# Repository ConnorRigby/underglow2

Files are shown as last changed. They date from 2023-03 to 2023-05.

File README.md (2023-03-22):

# Underglow 2

Automotive PMU designed for controlling external lighting.

## Specs

|high side output|low side output|12v digital input|BLE|Radio|
|-|-|-|-|-|
|2|6|4|1|1|

## Repository Structure

|folder|description|
|-|-|
|[docs](docs/README.md)|Documentation for hardware as well as 3d models and interactive bill of materials|
|[hardware](hardware/README.md)|Source material for the hardware PCB design|

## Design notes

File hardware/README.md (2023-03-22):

# coneRGB Underglow Controller Hardware Design

Source material for the PCB design. Designed using KiCAD intended to
be produced at PCBWay using parts from LCSC.

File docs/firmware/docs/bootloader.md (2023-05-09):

# coneRGB STM32 Bootloader

To facilitate over the air updates, coneRGB implements a custom bootloader.

```puml
@startuml
(*) --> "Power On Reset"

if "Update Status" then
  -left-> [started]"Enter Bootloader"
  --> copy update into flash
  -right->[jump to main application] (*)
else
  ->[no update] "Increment boot counter"
  -->[jump to main application] (*)
endif

@enduml
```

## Over The Air Update Procedure

* Initiate a firmware update over a supported transport (BLE, CAN)
* Write the entire update binary
* Initiate a reset
* The bootloader will now copy the update payload into flash

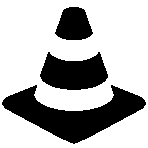
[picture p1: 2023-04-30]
assets/traffic-cone.bmp

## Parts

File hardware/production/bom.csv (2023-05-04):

Designator | Footprint | Quantity | Value | LCSC Part #
ANT601, ANT801 | IPEX-SMD_BWIPX-1-001E | 2 | BWIPX-1-001E | C496552
BT501 | BAT-SMD_CR1220-2 | 1 | Battery_Cell | C70381
C201, C301, C302, C303, C304, C305, C306, C307, C308, C309, C310, C605, C816 | 805 | 13 | C_0805_10u_X5R | C162422
C202, C603 | 805 | 2 | C_0805_1u_X7R | C24123
C401, C402, C502, C503, C504, C505, C506, C507, C508, C509, C511, C516, C519, C520, C521, C606, C607, C610, C611, C612, C808, C809, C810, C813 | 402 | 24 | C_0402_100nf_X7R | C110251
C501 | 805 | 1 | C_0805_4u7_X5R | C577033
C510 | 402 | 1 | C_0402_1u_X5R | C307413
C512, C513 | 402 | 2 | C_0402_2u2_X5R | C385032
C514, C515, C517, C518, C615, C616, C617, C618, C803, C811, C812 | 402 | 11 | C_0402_22p_C0G | C161315
C604, C801 | 402 | 2 | C_0402_10n_C0G | C60133
C608, C609 | 402 | 2 | C_0402_1p8_C0G | C76903
C802 | 402 | 1 | C_0402_8p2_C0G | C88898
C805 | 402 | 1 | C_0402_6p8_C0G | C354360
C807 | 402 | 1 | C_0402_3p3_C0G | C76968
C814 | 402 | 1 | C_0402_5p6_C0G | C88895
C815, L803, L804 | 402 | 3 | L_0402_5n6 | C91626
C823, C825 | 402 | 2 | C_0402_100p_C0G | C711072
C828, C829 | 402 | 2 | C_0402_1nf_X7R | C126538
D201, D504, D506 | 603 | 3 | LED_0603_RED | C389517
D202, D301, D302, D505 | D_SOD-323F | 4 | 30v 230mv@100ma 1A | C146335
D501 | SOT-23 | 1 | BAT54C | C5184395
D502 | 603 | 1 | LED_0603_GREEN | C389519
D503 | 603 | 1 | LED_0603_YELLOW | C72038
F201 | 1206 | 1 | nSMD010 | C70065
FB501 | 402 | 1 | FerriteBead_Small | C102745
L601, L802 | 402 | 2 | L_0402_22n | C86129
L602 | 402 | 1 | L_0402_3n3 | C341785
L801 | 402 | 1 | L_0402_2n7 | C98058
Q202, Q301 | SOP-8_3.76x4.96mm_P1.27mm | 2 | AO4803A | C5224315
Q302, Q303, Q304 | SOT-23-6 | 3 | 8205A | C2762931
Q801 | SOT-23 | 1 | BC817 | C39828
R201, R602 | 603 | 2 | R_0603_499 | C137714
R203, R206 | 805 | 2 | R_0805_10k | C17414
R207 | 805 | 1 | R_0805_4k7 | C17673
R301, R302, R701, R703, R705, R707 | 603 | 6 | R_0603_100k | C335088
R401 | 1206 | 1 | R_1206_120 | C294122
R402, R503, R504, R505, R608, R805 | 402 | 6 | R_0402_10k | C2902636
R501, R802, R803 | 402 | 3 | R_0402_100k | C2984406
R502, R601, R804 | 402 | 3 | R_0402_0 | C102745
R506, R507, R508, R509 | 603 | 4 | R_0603_330 | C861328
R702, R704, R706, R708 | 603 | 4 | R_0603_20k | C319766
RN501, RN502, RN503, RN504 | R_Array_Concave_4x0402 | 4 | RA_0402_04_100 | C48442
U201 | SOT-23-5 | 1 | SPX3819M5-L-3-3_TR | C9055
U202, U301, U302, U303, U304, U305, U306, U307, U308 | SOT-23-5 | 9 | MCP1416 | C83775
U401 | SOIC-8_3.9x4.9mm_P1.27mm | 1 | TLE9251VSJXUMA1 | C189937
U501 | SOIC-8_5.23x5.23mm_P1.27mm | 1 | W25Q16JVSSIQ | C82317
U503 | LQFP-100_14x14mm_P0.5mm | 1 | STM32F407VGTx | C12345
U601 | QFN50P500X500X90-33N | 1 | ESP32-C3FH4 | C2858491
U801 | QFN-28-1EP_5x5mm_P0.5mm_EP3.75x3.75mm_ThermalVias | 1 | RF69 | C77220
U802 | SOT-23-6 | 1 | AS193-73LF | C6199
Y501 | Crystal_SMD_3225-4Pin_3.2x2.5mm | 1 | 25_Mhz | C9006
Y502, Y602 | Crystal_SMD_3215-2Pin_3.2x1.5mm | 2 | Q13FC1350000400 | C32346
Y601 | Crystal_SMD_3225-4Pin_3.2x2.5mm | 1 | 40_Mhz | C2901712
Y801 | Crystal_SMD_3225-4Pin_3.2x2.5mm | 1 | 32_Mhz | C9009

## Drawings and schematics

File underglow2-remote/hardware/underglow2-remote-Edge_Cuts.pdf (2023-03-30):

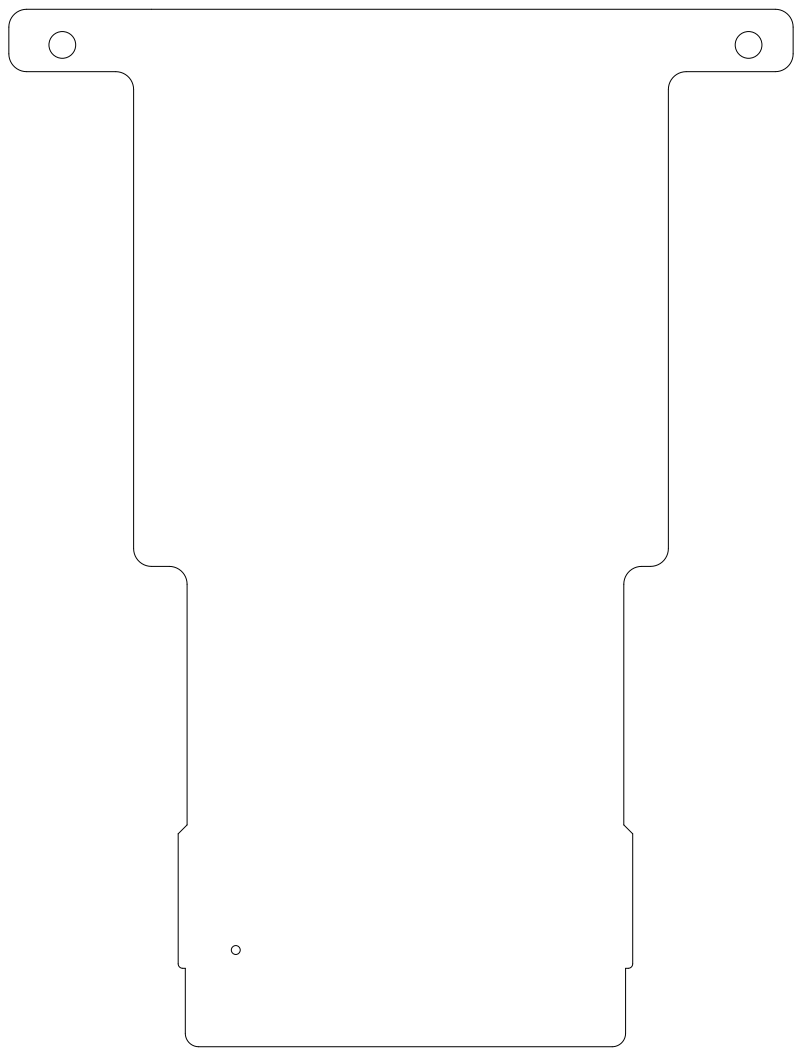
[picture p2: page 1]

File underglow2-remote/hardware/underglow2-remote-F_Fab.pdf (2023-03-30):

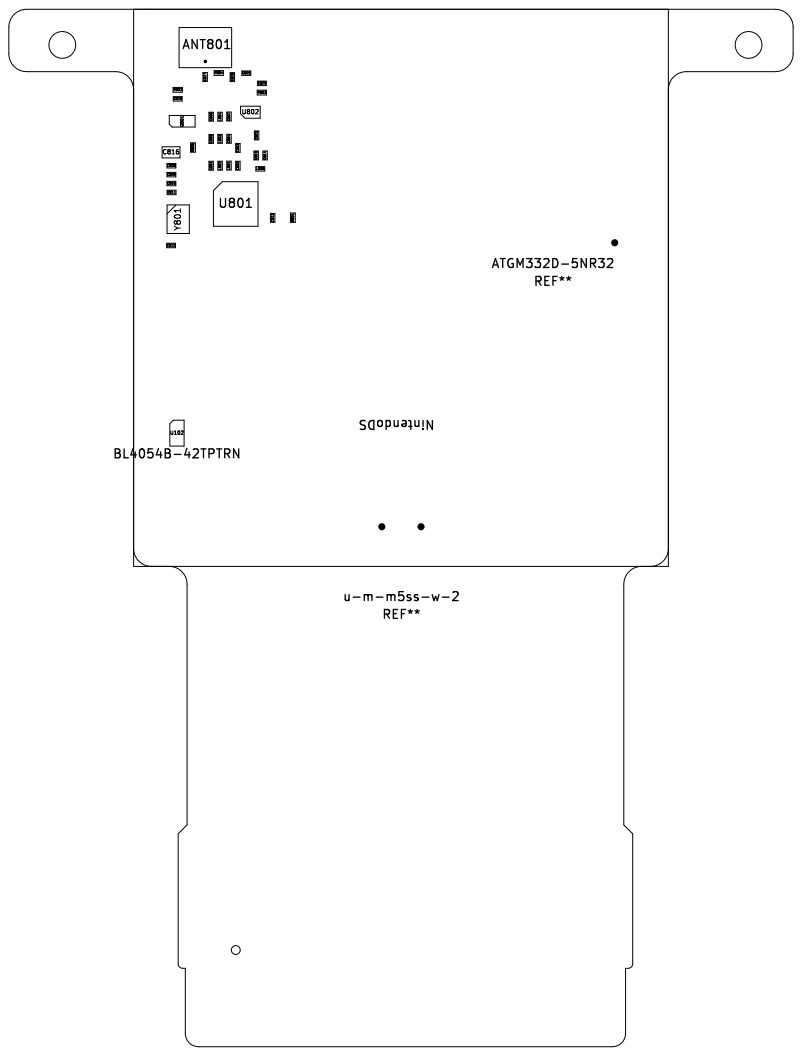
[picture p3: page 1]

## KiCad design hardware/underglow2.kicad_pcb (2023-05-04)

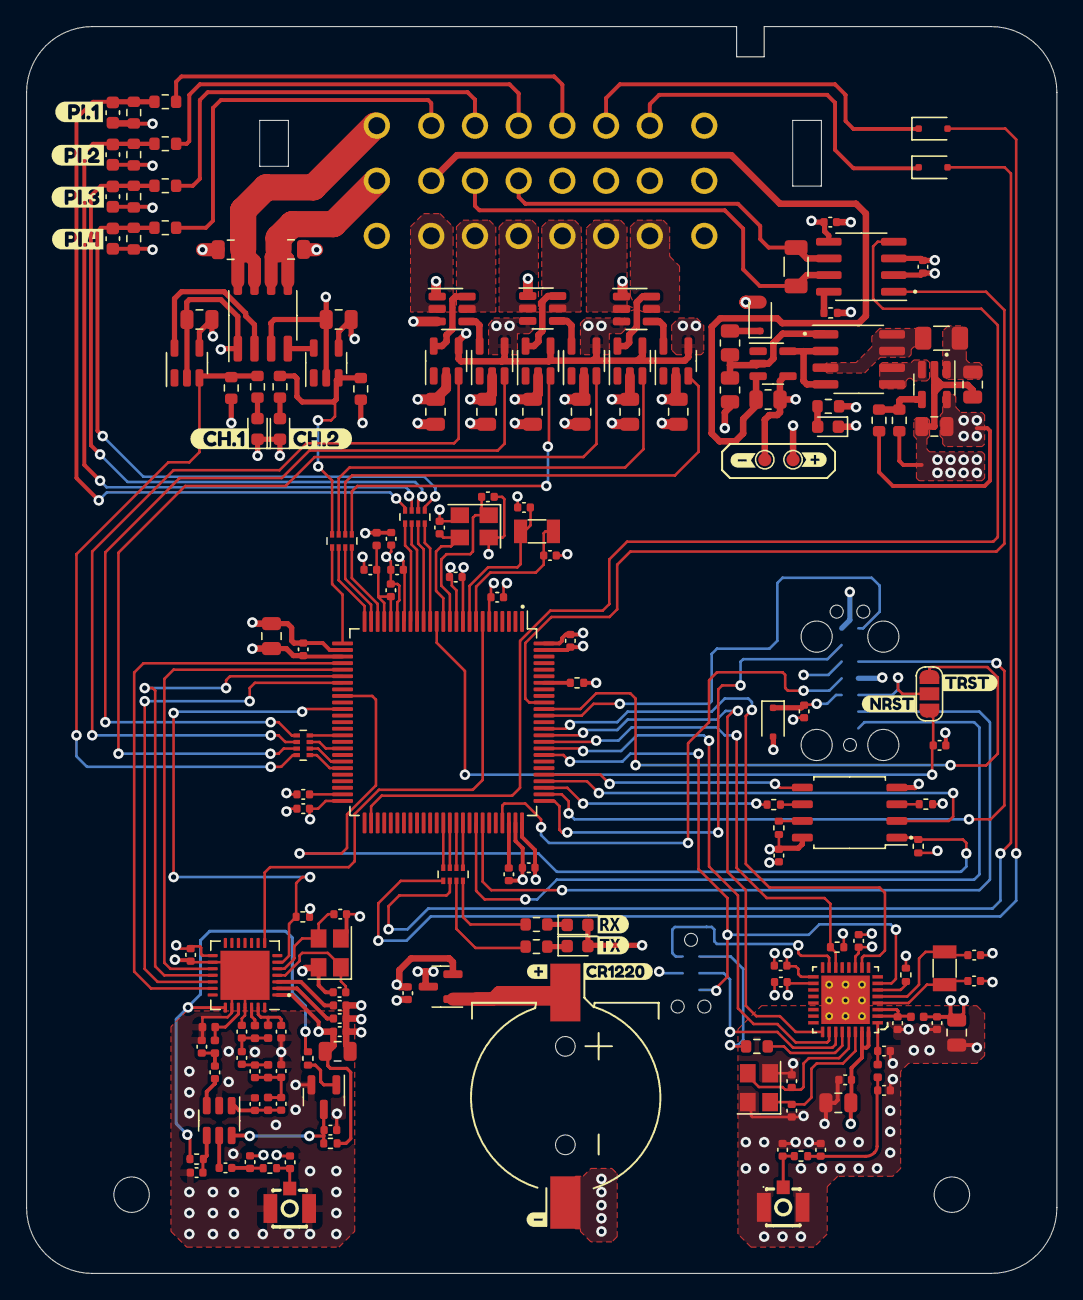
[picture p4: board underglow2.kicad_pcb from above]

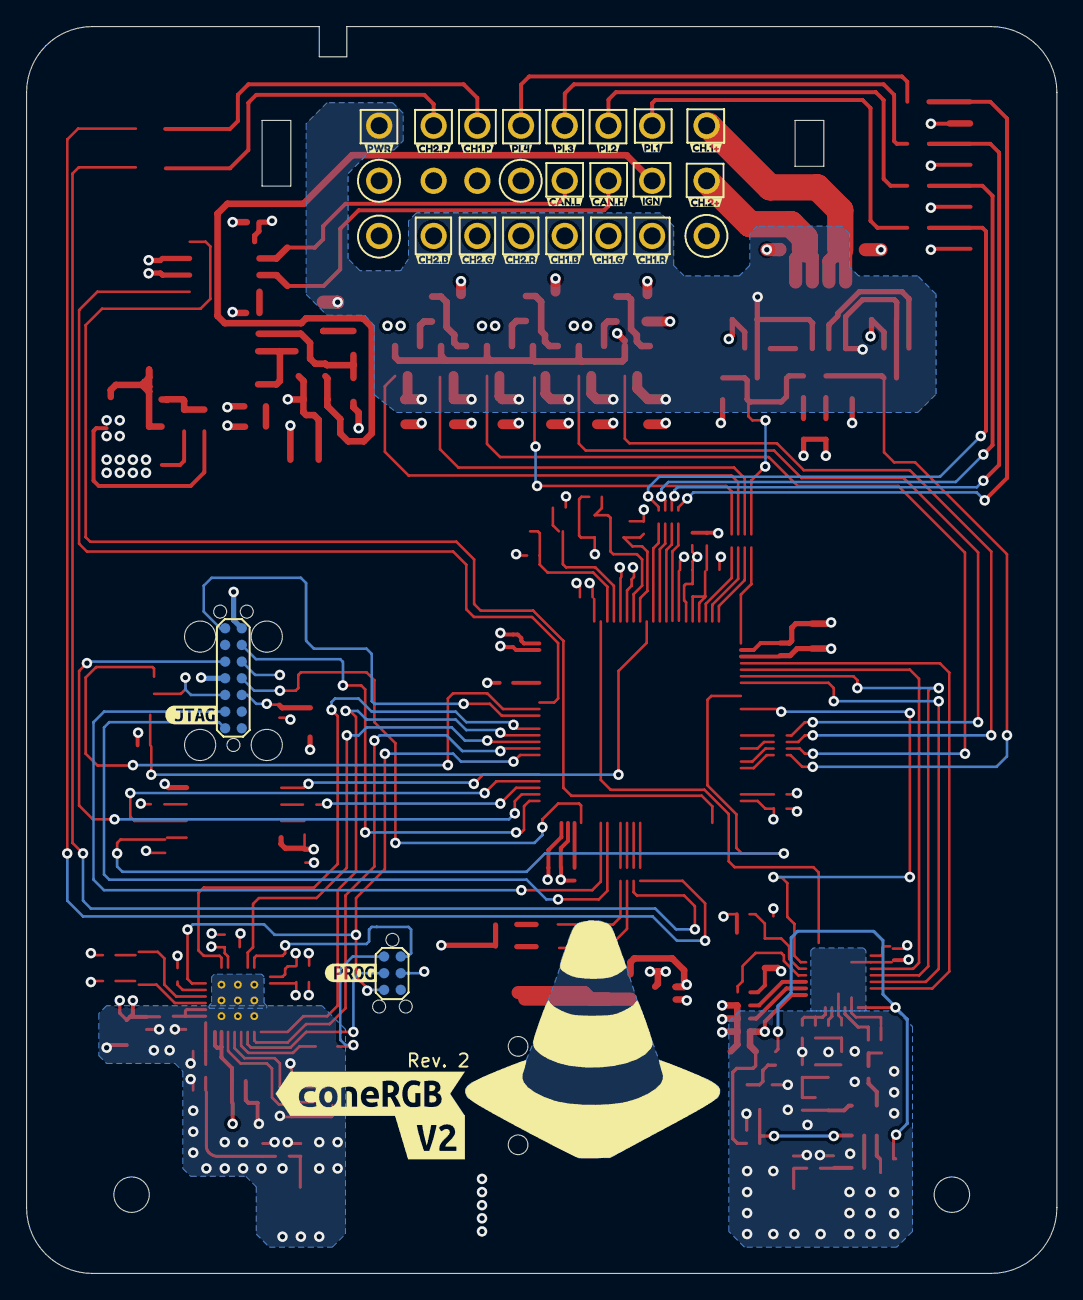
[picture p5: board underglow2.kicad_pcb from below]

Board: 4 copper layers, 78.5 x 95.0 mm, 214 parts (24 on the bottom side), 146 nets.

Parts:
ANT601, ANT801: BWIPX-1-001E; IPEX-SMD_BWIPX-1-001E
BT501: Battery_Cell; BAT-SMD_CR1220-2
Bottom: Case_Bottom; Bottom
C201, C301, C302, C303, C304, C305, C306, C307, C308, C309, C310, C605, C816: C_0805_10u_X5R; C_0805_2012Metric
C202, C603: C_0805_1u_X7R; C_0805_2012Metric
C401, C402, C502, C503, C504, C505, C506, C507, C508, C509, C511, C516, C519, C520, C521, C606, C607, C610, C611, C612, C808, C809, C810, C813: C_0402_100nf_X7R; C_0402_1005Metric
C501: C_0805_4u7_X5R; C_0805_2012Metric
C510: C_0402_1u_X5R; C_0402_1005Metric
C512, C513: C_0402_2u2_X5R; C_0402_1005Metric
C514, C515, C517, C518, C615, C616, C617, C618, C803, C811, C812: C_0402_22p_C0G; C_0402_1005Metric
C604, C801: C_0402_10n_C0G; C_0402_1005Metric
C608, C609: C_0402_1p8_C0G; C_0402_1005Metric
C613, C614, C804, C806, C826, C827: C_0402_DNP; C_0402_1005Metric
C701, C702, C703, C704: C_0603_DNP; C_0603_1608Metric
C802: C_0402_8p2_C0G; C_0402_1005Metric
C805: C_0402_6p8_C0G; C_0402_1005Metric
C807: C_0402_3p3_C0G; C_0402_1005Metric
C814: C_0402_5p6_C0G; C_0402_1005Metric
C815: L_0402_5n6; L_0402_1005Metric
C823, C825: C_0402_100p_C0G; C_0402_1005Metric
C828, C829: C_0402_1nf_X7R; C_0402_1005Metric
D201, D504, D506: LED_0603_RED; LED_0603_1608Metric
D202, D301, D302, D505: 30v 230mv@100ma 1A; D_SOD-323F
D501: BAT54C; SOT-23
D502: LED_0603_GREEN; LED_0603_1608Metric
D503: LED_0603_YELLOW; LED_0603_1608Metric
F201: nSMD010; Fuse_1206_3216Metric
FB501: FerriteBead_Small; L_0402_1005Metric
H1101, H1102: MountingHole_Pad; MountingHole_2.7mm_M2.5
J101: J_Delphi_Sicma_24; Delphi_Sicma_24_Black
J501: Conn_ST_STDC14; TC2070-IDC-FP
J601: Conn_02x03_Odd_Even; Tag-Connect_TC2030-IDC-NL_2x03_P1.27mm_Vertical
JP501: SolderJumper_3_Open; SolderJumper-3_P1.3mm_Open_RoundedPad1.0x1.5mm_NumberLabels
L601, L802: L_0402_22n; L_0402_1005Metric
L602: L_0402_3n3; L_0402_1005Metric
L801: L_0402_2n7; L_0402_1005Metric
L803, L804: L_0402_5n6; L_0402_1005Metric
L805: L_0402_120n; L_0402_1005Metric
Q202, Q301: AO4803A; SOP-8_3.76x4.96mm_P1.27mm
Q302, Q303, Q304: 8205A; SOT-23-6
Q801: BC817; SOT-23
R201, R602: R_0603_499; R_0603_1608Metric
R203, R206: R_0805_10k; R_0805_2012Metric
R204, R205: R_0603_DNP; R_0603_1608Metric
R207: R_0805_4k7; R_0805_2012Metric
R301, R302, R701, R703, R705, R707: R_0603_100k; R_0603_1608Metric
R401: R_1206_120; R_1206_3216Metric
R402, R503, R504, R505, R605, R608, R805: R_0402_10k; R_0402_1005Metric
R501, R801, R802, R803: R_0402_100k; R_0402_1005Metric
R502, R601, R804: R_0402_0; R_0402_1005Metric
R506, R507, R508, R509: R_0603_330; R_0603_1608Metric
R702, R704, R706, R708: R_0603_20k; R_0603_1608Metric
RN501, RN502, RN503, RN504: RA_0402_04_100; R_Array_Concave_4x0402
SMA_Connector: SMA_Connector_Antenna; SMA_Connector
TP201: 3.3v; TestPoint_Pad_D1.0mm
TP202: GND; TestPoint_Pad_D1.0mm
Top: Case_Top; Top
U201: SPX3819M5-L-3-3_TR; SOT-23-5
U202, U301, U302, U303, U304, U305, U306, U307, U308: MCP1416; SOT-23-5
U401: TLE9251VSJXUMA1; SOIC-8_3.9x4.9mm_P1.27mm
U501: W25Q16JVSSIQ; SOIC-8_5.23x5.23mm_P1.27mm
U503: STM32F407VGTx; LQFP-100_14x14mm_P0.5mm
U601: ESP32-C3FH4; QFN50P500X500X90-33N
U801: RF69; QFN-28-1EP_5x5mm_P0.5mm_EP3.75x3.75mm_ThermalVias
U802: AS193-73LF; SOT-23-6
Y501: 25_Mhz; Crystal_SMD_3225-4Pin_3.2x2.5mm
Y502, Y602: Q13FC1350000400; Crystal_SMD_3215-2Pin_3.2x1.5mm
Y601: 40_Mhz; Crystal_SMD_3225-4Pin_3.2x2.5mm
Y801: 32_Mhz; Crystal_SMD_3225-4Pin_3.2x2.5mm
kibuzzard-6452FB22, kibuzzard-6452FB22#2: G***; kibuzzard-6452FB22
kibuzzard-64531F0A: G***; kibuzzard-64531F0A
kibuzzard-64532A4E: G***; kibuzzard-64532A4E
kibuzzard-64532A7F: G***; kibuzzard-64532A7F
kibuzzard-64532A8F: G***; kibuzzard-64532A8F
kibuzzard-64532ABD: G***; kibuzzard-64532ABD
kibuzzard-64532AD1: G***; kibuzzard-64532AD1
kibuzzard-64532B0C: G***; kibuzzard-64532B0C
kibuzzard-64532B5A: G***; kibuzzard-64532B5A
kibuzzard-64532B45: G***; kibuzzard-64532B45
kibuzzard-64532B68: G***; kibuzzard-64532B68
kibuzzard-64532B76: G***; kibuzzard-64532B76
kibuzzard-64532BD6: G***; kibuzzard-64532BD6
kibuzzard-64532BFE: G***; kibuzzard-64532BFE
kibuzzard-64532C90: G***; kibuzzard-64532C90
kibuzzard-64532C97: G***; kibuzzard-64532C97
kibuzzard-64532CBD: G***; kibuzzard-64532CBD
kibuzzard-645321B8: G***; kibuzzard-645321B8
kibuzzard-645323AD: G***; kibuzzard-645323AD
kibuzzard-645327DB: G***; kibuzzard-645327DB
kibuzzard-645328AB: G***; kibuzzard-645328AB
kibuzzard-6415457F: G***; kibuzzard-6415457F
kibuzzard-6453207C: G***; kibuzzard-6453207C
kibuzzard-6453222E: G***; kibuzzard-6453222E
kibuzzard-6453280C: G***; kibuzzard-6453280C
kibuzzard-6453288C: G***; kibuzzard-6453288C
kibuzzard-6453293E: G***; kibuzzard-6453293E
kibuzzard-6453294D: G***; kibuzzard-6453294D
kibuzzard-64154474: G***; kibuzzard-64154474
kibuzzard-64532244: G***; kibuzzard-64532244
kibuzzard-64532252: G***; kibuzzard-64532252
kibuzzard-64532277: G***; kibuzzard-64532277
kibuzzard-64532290: G***; kibuzzard-64532290
kibuzzard-64532356: G***; kibuzzard-64532356
kibuzzard-64532361: G***; kibuzzard-64532361
kibuzzard-64532927: G***; kibuzzard-64532927

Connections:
+12V: C301.2, C302.2, C303.2, C304.2, C305.2, C306.2, C307.2, C308.2, D202.2 (A), J101.C8, Q301.1 (S), Q301.3 (S), U301.2 (Vdd), U302.2 (Vdd), U303.2 (Vdd), U304.2 (Vdd), U305.2 (Vdd), U306.2 (Vdd), U307.2 (Vdd), U308.2 (Vdd)
+BATT: C509.1, C612.1, C813.1, D501.3, U503.6 (VBAT), U601.11 (VDD3P3_RTC), U801.15 (VBAT2)
/Application/BOOT0: R501.1, U503.94 (BOOT0)
/Application/CAN_RX: U401.1 (TxD), U503.91 (PB5)
/Application/CAN_TX: U401.4 (RxD), U503.52 (PB13)
/Application/CH1_B_PWM: RN502.7 (R2.2), U303.3 (IN)
/Application/CH1_EN_PWM: R301.1, R508.2, RN502.8 (R1.2), U307.3 (IN)
/Application/CH1_G_PWM: RN502.6 (R3.2), U302.3 (IN)
/Application/CH1_NZR: D301.2 (A), RN503.1 (R1.1)
/Application/CH1_R_PWM: RN502.5 (R4.2), U301.3 (IN)
/Application/CH2_B_PWM: RN501.7 (R2.2), U306.3 (IN)
/Application/CH2_EN_PWM: R302.1, R509.2, RN501.8 (R1.2), U308.3 (IN)
/Application/CH2_G_PWM: RN501.6 (R3.2), U305.3 (IN)
/Application/CH2_NZR: D302.2 (A), RN503.2 (R2.1)
/Application/CH2_R_PWM: RN501.5 (R4.2), U304.3 (IN)
/Application/FLASH_HOLD: R505.2, U501.7 (IO3)
/Application/FLASH_SCK: R502.1, U501.6 (CLK)
/Application/FLASH_WP: R504.2, U501.3 (IO2)
/Application/GPIO_EXTI0: RN504.8 (R1.2), U503.15 (PC0)
/Application/GPIO_EXTI1: RN504.7 (R2.2), U503.16 (PC1)
/Application/GPIO_EXTI2: RN504.6 (R3.2), U503.17 (PC2)
/Application/GPIO_EXTI3: RN504.5 (R4.2), U503.18 (PC3)
/Application/HCI_CTS: U503.84 (PD3), U601.26 (GPIO19)
/Application/HCI_RTS: R605.1, U503.85 (PD4), U601.14 (GPIO8)
/Application/HCI_RX: U503.87 (PD6), U601.10 (MTDI)
/Application/HCI_TX: U503.86 (PD5), U601.25 (GPIO18)
/Application/PI1: C701.1, R701.2, R702.2, RN504.1 (R1.1)
/Application/PI2: C702.1, R703.2, R704.2, RN504.2 (R2.1)
/Application/PI3: C703.1, R705.2, R706.2, RN504.3 (R3.1)
/Application/PI4: C704.1, R707.2, R708.2, RN504.4 (R4.1)
/Application/RADIO_IRQ: U503.7 (PC13), U801.8 (DIO0)
/Application/RADIO_MISO: U503.31 (PA6), U801.18 (MISO)
/Application/RADIO_MOSI: U503.32 (PA7), U801.19 (MOSI)
/Application/RADIO_NSS: U503.29 (PA4), U801.20 (NSS)
/Application/RADIO_SCK: U503.30 (PA5), U801.17 (SCK)
/Application/RCC_OSC32_IN: C518.2, U503.8 (PC14), Y502.1
/Application/RCC_OSC32_OUT: C517.2, U503.9 (PC15), Y502.2
/Application/RCC_OSC_IN: C514.2, U503.12 (PH0), Y501.1
/Application/RCC_OSC_OUT: C515.2, U503.13 (PH1), Y501.3
/Application/SPI3_MISO: U501.2 (DO(IO1)), U503.79 (PC11)
/Application/SPI3_MOSI: U501.5 (DI(IO0)), U503.80 (PC12)
/Application/SPI3_NSS: R503.2, U501.1 (~CS), U503.34 (PC5)
/Application/SPI3_SCK: R502.2, U503.78 (PC10)
/Application/STATUS_RX: D503.1 (K), R507.2
/Application/STATUS_RX_1: R507.1, RN503.4 (R4.1)
/Application/STATUS_TX: D502.1 (K), R506.2
/Application/STATUS_TX_1: R506.1, RN503.3 (R3.1)
/Application/SYS_JTCK: J501.6 (JCLK/SWCLK), U503.76 (PA14)
/Application/SYS_JTDI: J501.10 (JTDI/NC), U503.77 (PA15)
/Application/SYS_JTDO: J501.8 (JTDO/SWO), U503.89 (PB3)
/Application/SYS_JTMS: J501.4 (JTMS/SWDIO), U503.72 (PA13)
/Application/SYS_TRST: JP501.1 (A), U503.90 (PB4)
/Application/TIM1_CH1: RN502.4 (R4.1), U503.40 (PE9)
/Application/TIM1_CH2: RN502.3 (R3.1), U503.42 (PE11)
/Application/TIM1_CH3: RN502.2 (R2.1), U503.44 (PE13)
/Application/TIM1_CH4: RN502.1 (R1.1), U503.45 (PE14)
/Application/TIM2_CH1: RN501.4 (R4.1), U503.23 (PA0)
/Application/TIM2_CH2: RN501.3 (R3.1), U503.24 (PA1)
/Application/TIM2_CH3: RN501.2 (R2.1), U503.25 (PA2)
/Application/TIM2_CH4: RN501.1 (R1.1), U503.26 (PA3)
/Application/TIM3_CH1: RN503.8 (R1.2), U503.63 (PC6)
/Application/TIM3_CH2: RN503.7 (R2.2), U503.64 (PC7)
/Application/TIM3_CH3: RN503.6 (R3.2), U503.65 (PC8)
/Application/TIM3_CH4: RN503.5 (R4.2), U503.66 (PC9)
/Application/USART1_RX: J501.13 (VCP_RX), U503.69 (PA10)
/Application/USART1_TX: J501.14 (VCP_TX), U503.68 (PA9)
/Application/VBAT: BT501.1 (+), D501.1
/Application/VCAP1: C512.2, U503.49 (VCAP_1)
/Application/VCAP2: C513.2, U503.73 (VCAP_2)
/Application/~DEBUG_RST: J501.12 (~RST), JP501.2 (C)
/Application/~RADIO_RESET: R801.2, U503.36 (PB1), U801.6 (RESET)
/Application/~RST: C516.1, JP501.3 (B), U503.14 (NRST)
/BLE/BLE_ANT: ANT601.1 (SIG), C614.2, R601.2
/BLE/BT_ANT: C608.1, C613.2, L602.2, R601.1
/BLE/GPIO2: R608.1, U601.6 (GPIO2)
/BLE/GPIO9: J601.2, U601.15 (GPIO9)
/BLE/HCI_EN: J601.5, U503.83 (PD2), U601.7 (CHIP_EN)
/BLE/LNA_IN: C609.1, L602.1, U601.1 (LNA_IN)
/BLE/RXD: J601.3, U601.27 (U0RXD)
/BLE/TXD: J601.1, R602.2
/BLE/TXD_1: R602.1, U601.28 (U0TXD)
/BLE/VDD3P3: C607.1, L601.1, U601.2 (VDD3P3), U601.3 (VDD3P3)
/BLE/XTALN: C616.2, U601.29 (XTAL_N), Y601.3
/BLE/XTALP: C615.2, U601.30 (XTAL_P), Y601.1
/BLE/XTAL_32K_N: C618.2, U601.5 (XTAL_32K_N), Y602.1
/BLE/XTAL_32K_P: C617.2, U601.4 (XTAL_32K_P), Y602.2
/CAN/CAN_H: J101.B3, R401.2, U401.7 (CANH)
/CAN/CAN_L: J101.B4, R401.1, U401.6 (CANL)
/CAN/STB: R402.1, U401.8 (STB)
/Digital Input/DI_1: J101.C2, R701.1
/Digital Input/DI_2: J101.C3, R703.1
/Digital Input/DI_3: J101.C4, R705.1
/Digital Input/DI_4: J101.C5, R707.1
/Power/BYP: R204.2, R205.1, U201.4 (BYP)
/Power/EN: J101.B2, R206.2, U202.3 (IN)
/Power/VIN: C201.1, F201.2, U201.1 (IN)
/Power/VIN_DIODE: D202.1 (K), R207.1
/Power/VIN_DIV: Q202.1 (S), R203.1, R207.2, U202.2 (Vdd)
/Power/VIN_GATE: Q202.2 (G), Q202.4 (G), U202.5 (OUT)
/RGB/PIXEL_1: D301.1 (K), J101.C6
/RGB/PIXEL_2: D302.1 (K), J101.C7
/RGB/RGB1_12V: C309.2, J101.C1, Q301.7 (D), Q301.8 (G)
/RGB/RGB1_B: J101.A4, Q303.2 (D)
/RGB/RGB1_B_GATE: Q303.4 (G), U303.5 (OUT)
/RGB/RGB1_G: J101.A3, Q302.5 (D)
/RGB/RGB1_GATE: Q301.2 (G), U307.5 (OUT)
/RGB/RGB1_G_GATE: Q302.6 (G), U302.5 (OUT)
/RGB/RGB1_R: J101.A2, Q302.2 (D)
/RGB/RGB1_R_GATE: Q302.4 (G), U301.5 (OUT)
/RGB/RGB2_12V: C310.2, J101.B1, Q301.5 (D), Q301.6 (G)
/RGB/RGB2_B: J101.A7, Q304.5 (D)
/RGB/RGB2_B_GATE: Q304.6 (G), U306.5 (OUT)
/RGB/RGB2_G: J101.A6, Q304.2 (D)
/RGB/RGB2_GATE: Q301.4 (G), U308.5 (OUT)
/RGB/RGB2_G_GATE: Q304.4 (G), U305.5 (OUT)
/RGB/RGB2_R: J101.A5, Q303.5 (D)
/RGB/RGB2_R_GATE: Q303.6 (G), U304.5 (OUT)
/Radio/J1: C825.1, U802.5 (J1)
/Radio/J2: C806.2, C807.2, L804.2, U802.1 (J2)
/Radio/J3: C823.2, U802.3 (J3)
/Radio/PA_BOOST: L801.1, U801.26 (PA_BOOST)
/Radio/PA_BOOST_PA: C802.1, C803.1, L801.2, L802.2
/Radio/PA_BOOST_PA_FILTER: C804.2, C805.2, C806.1, L803.2, L804.1
/Radio/PA_BOOST_PA_MATCH: C803.2, C804.1, L803.1
/Radio/RF69_ANTENNA: ANT801.1 (SIG), C827.2, R804.2
/Radio/RF69_ANT_MATCH: C825.2, C826.2, R804.1
/Radio/RFIO_MATCH: C814.1, C815.1, C823.1
/Radio/RF_IO: C815.2, L805.2, U801.24 (RFIO)
/Radio/RXTX: R803.1, R805.1, U801.22 (RXTX)
/Radio/RXTX_NOR: Q801.1 (B), R805.2
/Radio/V1: C828.2, Q801.3 (C), R802.2, U802.6 (V1)
/Radio/V2: C829.2, R803.2, U802.4 (V2)
/Radio/VR_ANA: C809.1, U801.2 (VR_ANA)
/Radio/VR_DIG: C810.1, U801.3 (VR_DIG)
/Radio/VR_PA: C801.1, L802.1, U801.27 (VR_PA)
/Radio/XTA: C811.2, U801.4 (XTA), Y801.1
/Radio/XTB: C812.2, U801.5 (XTB), Y801.3
GND: ANT601.2 (GND), ANT601.3 (GND), ANT801.2 (GND), ANT801.3 (GND), BT501.2 (-), C201.2, C202.2, C301.1, C302.1, C303.1, C304.1, C305.1, C306.1, C307.1, C308.1, C309.1, C310.1, C401.2, C402.2, C501.2, C502.2, C503.2, C504.2, C505.2, C506.2, C507.2, C508.2, C509.2, C510.2, C511.2, C512.1, C513.1, C514.1, C515.1, C516.2, C517.1, C518.1, C519.2, C520.2, C521.2, C603.2, C604.2, C605.2, C606.2, C607.2, C608.2, C609.2, C610.2, C611.2, C612.2, C613.1, C614.1, C615.1, C616.1, C617.1, C618.1, C701.2, C702.2, C703.2, C704.2, C801.2, C802.2, C805.1, C807.1, C808.2, C809.2, C810.2, C811.1, C812.1, C813.2, C814.2, C816.2, C826.1, C827.1, C828.1, C829.1, D201.1 (K), J101.A1, J101.A8, J101.B5, J101.B8, J501.5 (GND), J501.7 (GND), J501.11 (GNDDetect), J601.4, L805.1, Q302.1 (S), Q302.3 (S), Q303.1 (S), Q303.3 (S), Q304.1 (S), Q304.3 (S), Q801.2 (E), R203.2, R205.2, R206.1, R301.2, R302.2, R402.2, R501.2, R608.2, R702.1, R704.1, R706.1, R708.1, TP202.1, U201.2 (GND), U202.4 (GND), U301.4 (GND), U302.4 (GND), U303.4 (GND), U304.4 (GND), U305.4 (GND), U306.4 (GND), U307.4 (GND), U308.4 (GND), U401.2 (GND), U501.4 (GND), U503.10 (VSS), U503.20 (VSSA), U503.27 (VSS), U503.74 (VSS), U503.99 (VSS), U601.33 (GND), U801.16 (GND), U801.23 (GND), U801.25 (GND), U801.29 (PAD), U802.2 (GND), Y501.2, Y501.4, Y601.2, Y601.4, Y801.2, Y801.4
unnamed: C520.1, D505.1 (K), J501.3 (VCC)
unnamed: D201.2 (A), R201.2
unnamed: D504.2 (A), R509.1
unnamed: D506.2 (A), R508.1
unnamed: F201.1, Q202.3 (S), Q202.7 (D), Q202.8 (G)
unnamed: Q202.5 (D), Q202.6 (G), U201.3 (EN)
VDD: C202.1, C401.1, C402.1, C501.1, C502.1, C503.1, C504.1, C505.1, C506.1, C507.1, C508.1, C510.1, C521.1, C603.1, C604.1, C605.1, C606.1, C610.1, C611.1, C808.1, C816.1, D501.2, D502.2 (A), D503.2 (A), D504.1 (K), D505.2 (A), D506.1 (K), FB501.2, L601.2, R201.1, R204.1, R503.1, R504.1, R505.1, R605.2, R801.1, R802.1, TP201.1, U201.5 (OUT), U401.3 (VCC), U401.5 (VIO), U501.8 (VCC), U503.11 (VDD), U503.19 (VDD), U503.28 (VDD), U503.50 (VDD), U503.75 (VDD), U503.100 (VDD), U601.17 (VDD3P3_CPU), U601.18 (VDD_SPI), U601.31 (VDDA), U601.32 (VDDA), U801.1 (VBAT1)
VDDA: C511.1, C519.1, FB501.1, U503.21 (VREF+), U503.22 (VDDA)

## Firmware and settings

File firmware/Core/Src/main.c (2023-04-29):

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
/* Includes ------------------------------------------------------------------*/
#include "main.h"

/* USER CODE BEGIN Includes */
// #include "port.h"
/* USER CODE END Includes */

FDCAN_HandleTypeDef hfdcan1;

UART_HandleTypeDef hlpuart1;
UART_HandleTypeDef huart1;
DMA_HandleTypeDef hdma_lpuart1_rx;
DMA_HandleTypeDef hdma_lpuart1_tx;

SPI_HandleTypeDef hspi1;

TIM_HandleTypeDef htim1;
TIM_HandleTypeDef htim2;
TIM_HandleTypeDef htim3;
TIM_HandleTypeDef htim8;
DMA_HandleTypeDef hdma_tim2_ch2;
DMA_HandleTypeDef hdma_tim3_ch1;
DMA_HandleTypeDef hdma_tim8_ch1;

PCD_HandleTypeDef hpcd_USB_FS;

/* USER CODE BEGIN PV */
void btstack_port(void);
/* USER CODE END PV */

void SystemClock_Config(void);
static void MX_GPIO_Init(void);
static void MX_DMA_Init(void);
static void MX_FDCAN1_Init(void);
static void MX_LPUART1_UART_Init(void);
static void MX_USART1_UART_Init(void);
static void MX_SPI1_Init(void);
static void MX_TIM1_Init(void);
static void MX_TIM2_Init(void);
static void MX_TIM3_Init(void);
static void MX_TIM8_Init(void);
static void MX_USB_PCD_Init(void);
/* USER CODE BEGIN 0 */

#define RGB_LEN (24 * 10)
#define numberofpixels 10
#define bytesperpixel 3
#define bitHightimercount 58
#define bitLowtimercount 22

// #define bitHightimercount 120
// #define bitLowtimercount 30

uint32_t loadArrayOnePixel(uint8_t R, uint8_t G, uint8_t B,
		uint8_t *buffer, //address of our buffer
		uint8_t pixelnumber //pixel index inside buffer
		) {
	if(pixelnumber>numberofpixels){return -1;}//in case we mess up

	for (uint32_t i = 0; i < bytesperpixel * 8; ++i) { //we need to store every bit

		if (i < 8) { //this means first byte R
			if (R & (0x80 >> i)) { //this is a mask for reading every bit inside the byte R
				buffer[i + pixelnumber * bytesperpixel * 8] = bitHightimercount;
			} else {
				buffer[i + pixelnumber * bytesperpixel * 8] = bitLowtimercount;
			}
		}

		if ((i >= 8) & (i < 16)) { //this means second byte G
			if (G & (0x80 >> (i - 8))) {
				buffer[i + pixelnumber * bytesperpixel * 8] = bitHightimercount;
			} else {
				buffer[i + pixelnumber * bytesperpixel * 8] = bitLowtimercount;
			}
		}

		if ((i >= 16) & (i < 24)) { //this means third byte B
			if (B & (0x80 >> (i - 16))) {
				buffer[i + pixelnumber * bytesperpixel * 8] = bitHightimercount;
			} else {
				buffer[i + pixelnumber * bytesperpixel * 8] = bitLowtimercount;
			}
		}

	}
	return 1;
}

/* USER CODE END 0 */

/**
  * @brief  The application entry point.
  * @retval int
  */
int main(void)
{
  /* MCU Configuration--------------------------------------------------------*/

  /* Reset of all peripherals, Initializes the Flash interface and the Systick. */
  HAL_Init();

  /* Configure the system clock */
  SystemClock_Config();

  /* Initialize all configured peripherals */
  MX_GPIO_Init();
  MX_DMA_Init();
  MX_FDCAN1_Init();
  MX_LPUART1_UART_Init();
  MX_USART1_UART_Init();
  MX_SPI1_Init();
  MX_TIM1_Init();
  MX_TIM2_Init();
  MX_TIM3_Init();
  MX_TIM8_Init();
  MX_USB_PCD_Init();
  /* USER CODE BEGIN 2 */
  // TIM3->CCR1=77; // 64%
  // TIM3->CCR1=38; // 32%
  /*
  uint8_t rgb[RGB_LEN+1] = {
    // 1
    58, 58, 58, 58, 58, 58, 58, 58,
    22, 22, 22, 22, 22, 22, 22, 22,
    22, 22, 22, 22, 22, 22, 22, 22,
    // 2
    22, 22, 22, 22, 22, 22, 22, 22,
    58, 58, 58, 58, 58, 58, 58, 58,
    22, 22, 22, 22, 22, 22, 22, 22,
    // 3
    22, 22, 22, 22, 22, 22, 22, 22,
    22, 22, 22, 22, 22, 22, 22, 22,
    58, 58, 58, 58, 58, 58, 58, 58,
    // 4
    58, 58, 58, 58, 58, 58, 58, 58,
    22, 22, 22, 22, 22, 22, 22, 22,
    22, 22, 22, 22, 22, 22, 22, 22,
    // 5
    22, 22, 22, 22, 22, 22, 22, 22,
    58, 58, 58, 58, 58, 58, 58, 58,
    22, 22, 22, 22, 22, 22, 22, 22,
    // 6
    22, 22, 22, 22, 22, 22, 22, 22,
    22, 22, 22, 22, 22, 22, 22, 22,
    58, 58, 58, 58, 58, 58, 58, 58,
    // 7
    58, 58, 58, 58, 58, 58, 58, 58,
    22, 22, 22, 22, 22, 22, 22, 22,
    22, 22, 22, 22, 22, 22, 22, 22,
    // 8
    22, 22, 22, 22, 22, 22, 22, 22,
    58, 58, 58, 58, 58, 58, 58, 58,
    22, 22, 22, 22, 22, 22, 22, 22,
    // 9
    22, 22, 22, 22, 22, 22, 22, 22,
    22, 22, 22, 22, 22, 22, 22, 22,
    58, 58, 58, 58, 58, 58, 58, 58,
    // 10
    58, 58, 58, 58, 58, 58, 58, 58,
    22, 22, 22, 22, 22, 22, 22, 22,
    22, 22, 22, 22, 22, 22, 22, 22,
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
  };
  */
  uint8_t rgb[RGB_LEN + 1] = {0};
  for(int i = 0; i < RGB_LEN; i++) {
    rgb[i] = bitHightimercount;
  }
  rgb[RGB_LEN] = 0;
  // for (int i = 0; i < numberofpixels; ++i) {
  //     loadArrayOnePixel(0,0,255, &rgb, i);
  // }

	uint8_t counter=0;
	uint8_t flag=0;

  while(1) {
    HAL_TIM_PWM_Stop_DMA(&htim3, TIM_CHANNEL_1);
    for (int i = 0; i < numberofpixels; ++i) {
        loadArrayOnePixel(counter,0,counter, &rgb, i);
    }
    HAL_TIM_PWM_Start_DMA(&htim3, TIM_CHANNEL_1, rgb, sizeof(uint8_t) * RGB_LEN+1);

		if(counter==0xFF){flag=0;}

		if(counter==0x00){flag=1;}

		if(flag){
			counter++;
		}else{
			counter--;
		}

    HAL_Delay(10);
  }
  // port_main();
  entry();

  /* USER CODE END 2 */

  /* Infinite loop */
  /* USER CODE BEGIN WHILE */
  while (1)
  {
    /* USER CODE END WHILE */

    /* USER CODE BEGIN 3 */
  }
  /* USER CODE END 3 */
}

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


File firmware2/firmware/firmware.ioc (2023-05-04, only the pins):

PH0-OSC_IN.Signal=RCC_OSC_IN
Mcu.UserName=STM32F407VGTx
PE11.GPIO_Label=CH1_G
PC10.Signal=SPI3_SCK
PC12.Signal=SPI3_MOSI
PC0.GPIO_Label=PI1
PC6.GPIO_Label=CH2_NZR
PB13.Signal=CAN2_TX
PD6.GPIO_Label=HCI_RX
PD4.Signal=USART2_RTS
PC7.Signal=S_TIM3_CH2
PC3.Signal=SharedStack_PC3
PC13-ANTI_TAMP.Signal=GPXTI13
PE13.Signal=S_TIM1_CH3
PE9.Signal=S_TIM1_CH1
PA8.Signal=RCC_MCO_1
PA6.Signal=SPI1_MISO
PD5.GPIO_Label=HCI_TX
PA2.GPIO_Label=CH2_B
PA10.Signal=USART1_RX
PA15.Signal=SYS_JTDI
PD3.GPIO_Label=HCI_CTS
PD6.Signal=USART2_RX
PC2.GPIO_Label=PI3
PB4.Signal=SYS_JTRST
PA3.Signal=S_TIM2_CH4
PC13-ANTI_TAMP.GPIO_Label=RADIO_IRQ
PC11.Signal=SPI3_MISO
PD3.Signal=USART2_CTS
PC8.Signal=S_TIM3_CH3
PC2.Signal=SharedStack_PC2
PC6.Signal=S_TIM3_CH1
PE14.GPIO_Label=CH1_EN
PD5.Signal=USART2_TX
PC0.Signal=SharedStack_PC0
PC14-OSC32_IN.Signal=RCC_OSC32_IN
PA0-WKUP.GPIO_Label=CH2_R
PA0-WKUP.Signal=S_TIM2_CH1_ETR
PA13.Signal=SYS_JTMS-SWDIO
PA9.Signal=USART1_TX
PE11.Signal=S_TIM1_CH2
PC15-OSC32_OUT.Signal=RCC_OSC32_OUT
PE9.GPIO_Label=CH1_R
PA1.Signal=S_TIM2_CH2
PA5.Signal=SPI1_SCK
PE14.Signal=S_TIM1_CH4
PD4.GPIO_Label=HCI_RTS
PC1.GPIO_Label=PI2
PA1.GPIO_Label=CH2_G
PH1-OSC_OUT.Signal=RCC_OSC_OUT
PA2.Signal=S_TIM2_CH3
PC7.GPIO_Label=CH1_NZR
PB3.Signal=SYS_JTDO-SWO
PA4.Signal=SPI1_NSS
PB5.Signal=CAN2_RX
PE13.GPIO_Label=CH1_B
PA14.Signal=SYS_JTCK-SWCLK
PC3.GPIO_Label=PI4
PC9.Signal=S_TIM3_CH4
PC1.Signal=SharedStack_PC1
PA3.GPIO_Label=CH2_EN
PA7.Signal=SPI1_MOSI

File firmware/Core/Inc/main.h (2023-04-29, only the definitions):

#define CH2_NRZ_Pin GPIO_PIN_1
#define CH2_NRZ_GPIO_Port GPIOA
#define CH2_EN_Pin GPIO_PIN_2
#define CH2_EN_GPIO_Port GPIOA
#define CH1_EN_Pin GPIO_PIN_3
#define CH1_EN_GPIO_Port GPIOA
#define RF69_NSS_Pin GPIO_PIN_4
#define RF69_NSS_GPIO_Port GPIOA
#define RF69_SCK_Pin GPIO_PIN_5
#define RF69_SCK_GPIO_Port GPIOA
#define RF69_MISO_Pin GPIO_PIN_6
#define RF69_MISO_GPIO_Port GPIOA
#define CH1_R_Pin GPIO_PIN_7
#define CH1_R_GPIO_Port GPIOA
#define RF69_NRESET_Pin GPIO_PIN_0
#define RF69_NRESET_GPIO_Port GPIOB
#define CH2_R_Pin GPIO_PIN_1
#define CH2_R_GPIO_Port GPIOB
#define HCI_RX_Pin GPIO_PIN_10
#define HCI_RX_GPIO_Port GPIOB
#define HCI_TX_Pin GPIO_PIN_11
#define HCI_TX_GPIO_Port GPIOB
#define HCI_RTS_Pin GPIO_PIN_12
#define HCI_RTS_GPIO_Port GPIOB
#define HCI_CTS_Pin GPIO_PIN_13
#define HCI_CTS_GPIO_Port GPIOB
#define CH1_G_Pin GPIO_PIN_14
#define CH1_G_GPIO_Port GPIOB
#define CH1_B_Pin GPIO_PIN_15
#define CH1_B_GPIO_Port GPIOB
#define DI1_Pin GPIO_PIN_6
#define DI1_GPIO_Port GPIOC
#define DI1_EXTI_IRQn EXTI9_5_IRQn
#define DI2_Pin GPIO_PIN_8
#define DI2_GPIO_Port GPIOA
#define DI2_EXTI_IRQn EXTI9_5_IRQn
#define DI3_Pin GPIO_PIN_9
#define DI3_GPIO_Port GPIOA
#define DI3_EXTI_IRQn EXTI9_5_IRQn
#define DI4_Pin GPIO_PIN_15
#define DI4_GPIO_Port GPIOA
#define DI4_EXTI_IRQn EXTI15_10_IRQn
#define CH2_B_Pin GPIO_PIN_10
#define CH2_B_GPIO_Port GPIOC
#define CH2_G_Pin GPIO_PIN_11
#define CH2_G_GPIO_Port GPIOC
#define CH1_NRZ_Pin GPIO_PIN_4
#define CH1_NRZ_GPIO_Port GPIOB
#define RF69_MOSI_Pin GPIO_PIN_5
#define RF69_MOSI_GPIO_Port GPIOB
#define STATUS_LED_GREEN_TX_Pin GPIO_PIN_6
#define STATUS_LED_GREEN_TX_GPIO_Port GPIOB
#define STATUS_LED_YELLOW_RX_Pin GPIO_PIN_7
#define STATUS_LED_YELLOW_RX_GPIO_Port GPIOB

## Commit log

2023-03-01 Schematic progress
    [Application.kicad_sch, BLE.kicad_sch, CAN.kicad_sch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]
2023-03-01 Schematic updates: stm32 sheet
    [Application.kicad_sch, BLE.kicad_sch, CAN.kicad_sch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]
2023-03-11 Schematic and layout Progress
    [Application.kicad_sch, BLE.kicad_sch, CAN.kicad_sch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]
2023-03-13 Layout updates
    [Application.kicad_sch, BLE.kicad_sch, Digital-Input.kicad_sch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]
2023-03-13 Update layout
    [Application.kicad_sch, Radio.kicad_sch, underglow2.kicad_pcb]
2023-03-20 RF layout updates
    [RGB.kicad_sch, Radio.kicad_sch, underglow-controller-case-top.step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]
2023-03-20 Almost ready for fab
    [Application.kicad_sch, BLE.kicad_sch, Digital-Input.kicad_sch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]
2023-03-21 Pre-production updates
    [Application.kicad_sch, BLE.kicad_sch, CAN.kicad_sch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]
2023-03-21 Add Case and other models
    [underglow2.kicad_pcb]
2023-03-21 More pre-production updates:
    * fix USART connections being reversed
    * add test points for SPI and BLE
    [Application.kicad_sch, underglow2.kicad_pcb, underglow2.kicad_sch]
2023-03-22 Submitted for production
    [BLE.kicad_sch, Radio.kicad_sch, Unnamed-underglow2.3mf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]
2023-03-24 Add HALs for gpio and SPI
2023-03-25 CAN HAL driver
2023-03-28 Start adding a nds powered remote control
    [underglow2-remote-cart.kicad_pcb, underglow2-remote-cart.kicad_sch, underglow2-remote.kicad_pcb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]
2023-03-30 board layout testing for nds remote
    [Radio.kicad_sch, underglow2-remote.kicad_sch]
2023-04-05 Generate firmware for STM32G4
2023-04-10 Implement param framework for patterns
2023-04-17 hardware: Add flash storage
    [Application.kicad_sch, underglow2.kicad_pcb]
2023-04-17 hardware: add USB for debugging and programming
    [Application.kicad_sch, Power.kicad_sch, Radio.kicad_sch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]
2023-04-29 Implement basic neopixel driver
2023-05-04 Rev 2 submitted for production
    [Application.kicad_sch, BLE.kicad_sch, CAN.kicad_sch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]

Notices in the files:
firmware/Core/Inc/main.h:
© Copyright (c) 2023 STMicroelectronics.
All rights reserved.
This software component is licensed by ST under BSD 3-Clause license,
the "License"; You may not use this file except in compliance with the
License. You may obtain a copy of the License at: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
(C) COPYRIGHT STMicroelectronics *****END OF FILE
